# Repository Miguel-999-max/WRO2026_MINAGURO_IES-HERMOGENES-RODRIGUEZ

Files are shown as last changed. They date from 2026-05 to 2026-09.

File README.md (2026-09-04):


# WRO Future Engineers - MINAGURO
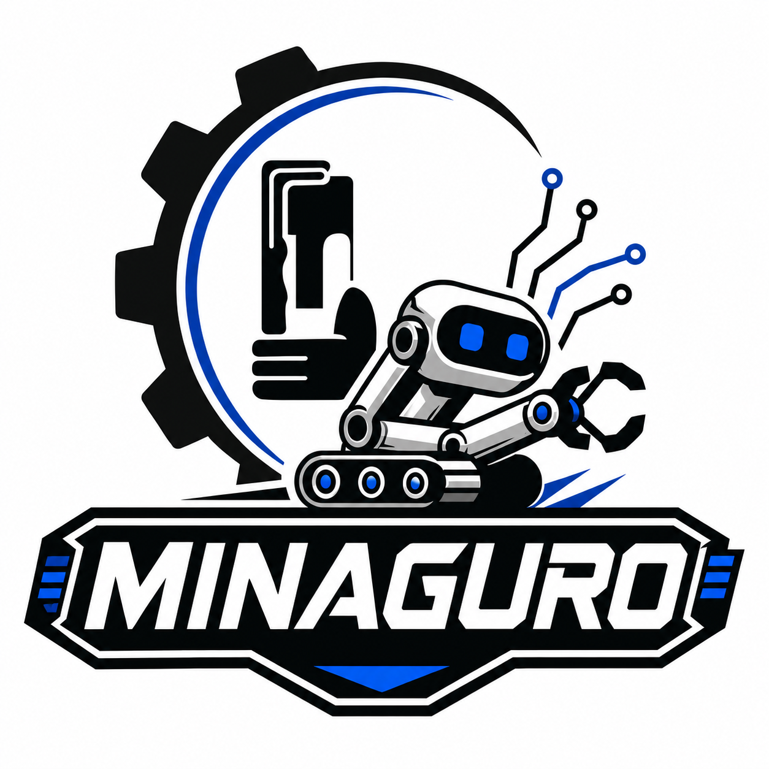
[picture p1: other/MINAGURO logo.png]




<div align="justify">Hello, welcome to the GitHub repository of the <strong>MINAGURO team</strong>, which is competing in the <strong>World Robot Olympiad 2026 Future Engineers</strong> category. Our team is made up of four Spanish students who develop this project on their school breaks with the aim of learning as much as possible.
<br> Guided by our passion for technology, we have created two vehicles. One (the old one), which helped us to get to de national final of the WRO in Andorra; and, another one (the current one), that will perform in the national final. We created the second one motivated by our desire to do it as good as possible and also learn new things and concepts along the way.
<br> Hope you like it!!
</div><br> </br>

> [!IMPORTANT]
> Every time you see this sign (▶&#xFE0E;), click on the text next to it to expand the content!

## 🤝 Sponsors
<div align="justify">We would like to thank our sponsors for making this project possible:

<div align="center">
  <table border="0">
    <tr>
      <td align="center" width="300">
        <a href="https://www.uclm.es/">
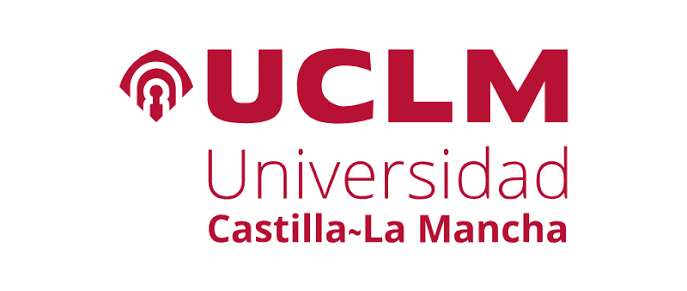
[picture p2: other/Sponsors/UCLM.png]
          <br />
          <b>Universidad de Castilla La Mancha</b>
        </a>
      </td>
      <td align="center" width="300">
        <a href="https://ies-hermogenesrodriguez.centros.castillalamancha.es/">
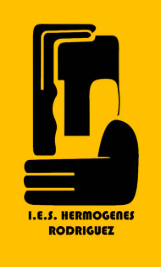
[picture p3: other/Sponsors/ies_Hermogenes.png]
          <br />
          <b>IES Hermógenes Rodríguez</b>
        </a>
      </td>
    </tr>
  </table>
</div>
 
  ## 📁 TABLE OF CONTENTS
* [1. 👥 The Team ](#1--the-team)
* [2. 🤖 Our Robot](#2--our-robot)
* [3. 📝 Daily documentation](#3--daily-documentation)
* [4. 🛠️ Mechanical Design](#seccion-mecanica)
* [5. 🪛 Mobility design](#5--mobility-design)
* [6. ⚡Power and Sensor Architecture](#6--power-and-sensor-architecture)
* [7. 🧠 Strategy](#7--strategy)
* [8. 💻 Software](#8--software)
* [9. 🦾 Build our robot](#9--build-our-robot)

### 1. 👥 The Team
The Minaguro team from Herencia, Spain, is made up of dedicated and hardworking members led by a teacher. This is our first year competing in the WRO Future Engineers category, and each member brings important skills to the team.

<div align="center"><table>
  <tr>
    <td align="center" width="50%">
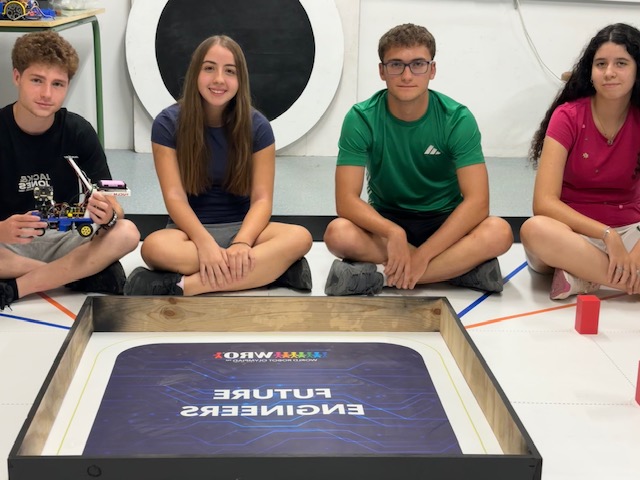
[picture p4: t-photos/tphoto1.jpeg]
      
     team photo
    </td>
    <td align="center" width="50%">
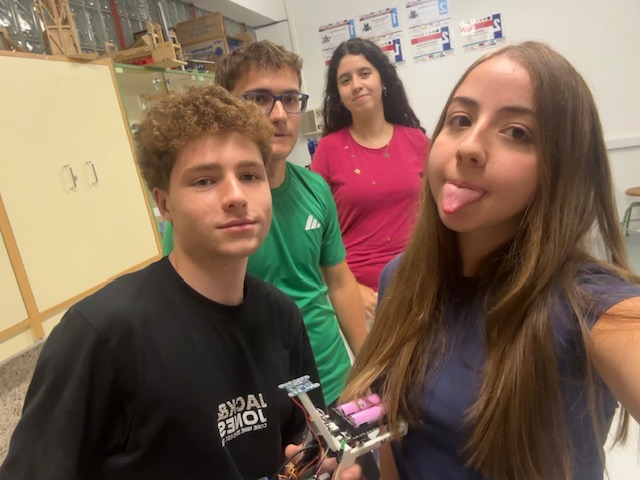
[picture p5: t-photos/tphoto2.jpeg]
      
     funny team photo
    </td>
  </tr>
</table></div>

<br> **Miguel**
<br> **Age:** 17
<br> **Description:** Hi, I'm Miguel from Ciudad Real, Spain, and this is my first time participating in WRO Competition. I have always been into mechanics and robot building, so I didn't hesistate to take up this challenge. I am such a curious and competitive person, and I had put all my efforts in helping the team.

<br> **Natalia**
<br> **Age:** 17
<br> **Description:** Hi, I am Natalia, also from Ciudad Real, Spain, and it is my first time participating, too. I am really good at programming, which I actually enjoy doing. I am hardworking and creative, and this competition, despite being really demanding, has helped me to enter the engineering world.

<br> **Rocío** 
<br> **Age:** 16
<br> **Description:** Hi! I'm Rocío from Spain and this is the first time in the WRO competition. Since I was a kid, I've loved solving puzzles and maths problems. I started to interest in robotics when I was at secondary school, when my teacher taught us how to program. I thougth that was really fun.

<br> **Guillermo**
<br> **Age:** 16
<br> **Description:** Hi, I am Guillermo. I am from Ciudad Real, Spain, and I joined this project because I have always been really keen on I.T. and problem solving. Although this competition has been really challenging, the experience with all the team is worth it.

### 2. 🤖 Our Robot

#### 2.1 Old Robot (Arduino)

<details>
<summary><b>Here are some pictures of our old robot to help with it´s reproducibility:</b></summary>
<br>

<div align="center"><table>
  <tr>
    <td align="center" width="33%">
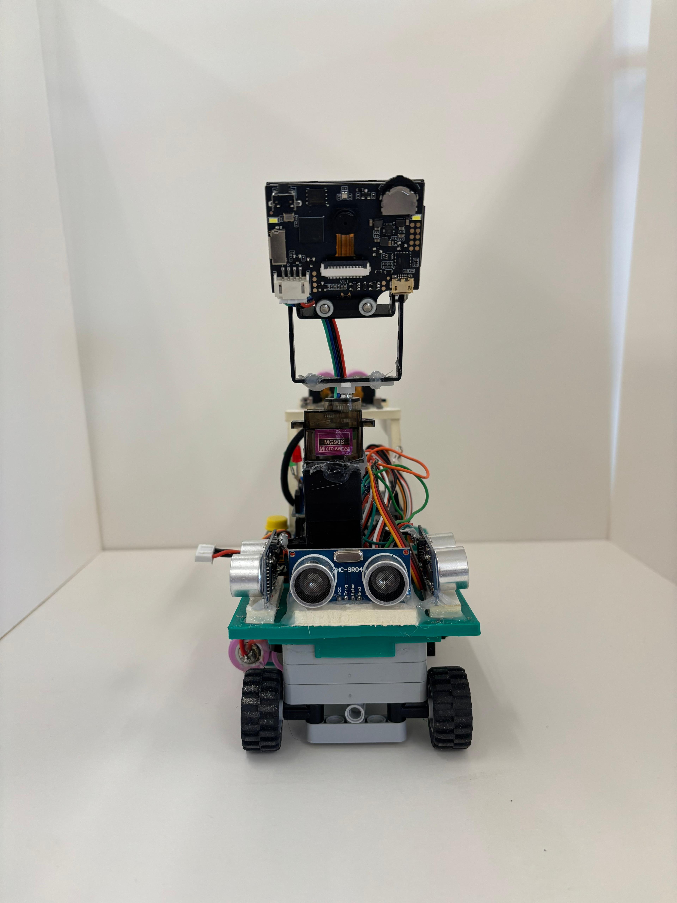
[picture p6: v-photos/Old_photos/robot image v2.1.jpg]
      
     robot´s front view
    </td>
    <td align="center" width="33%">
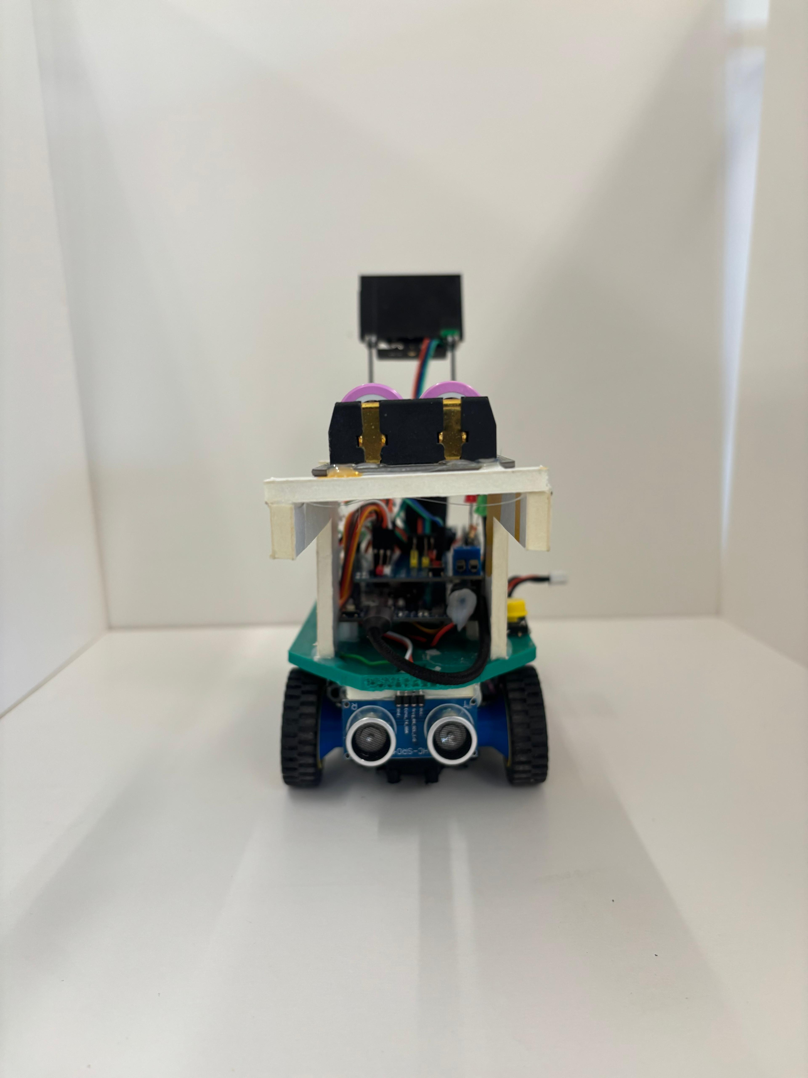
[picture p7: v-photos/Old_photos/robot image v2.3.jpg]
      
     robot´s back view
    </td>
    <td align="center" width="33%">
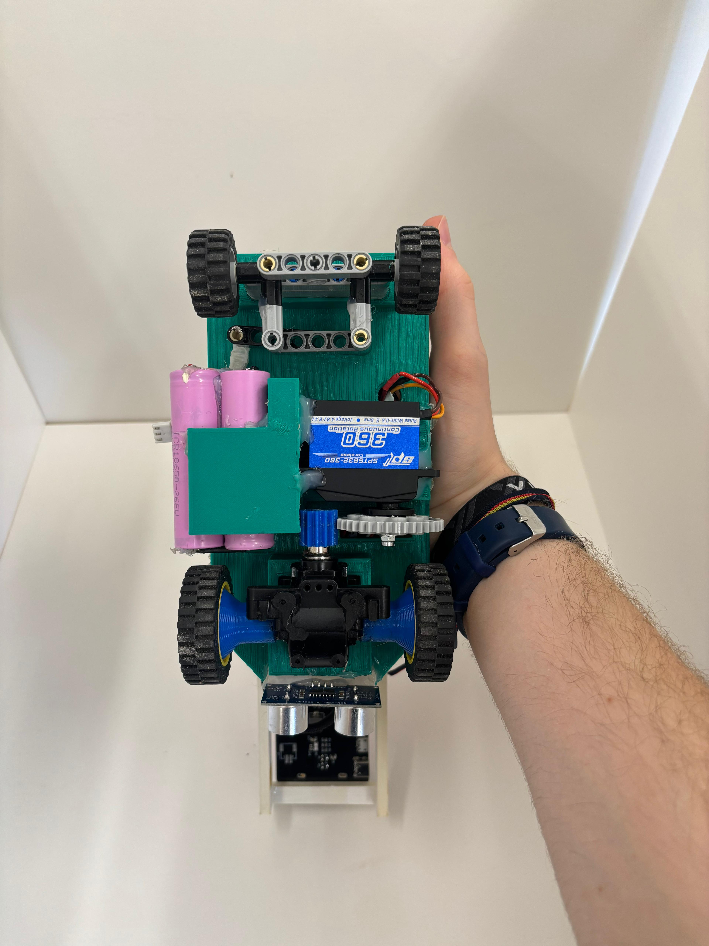
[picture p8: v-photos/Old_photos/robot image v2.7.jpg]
      
     View from underneath the robot
    </td>
  </tr>
</table></div>

<div align="center"><table>
  <tr>
    <td align="center" width="33%">
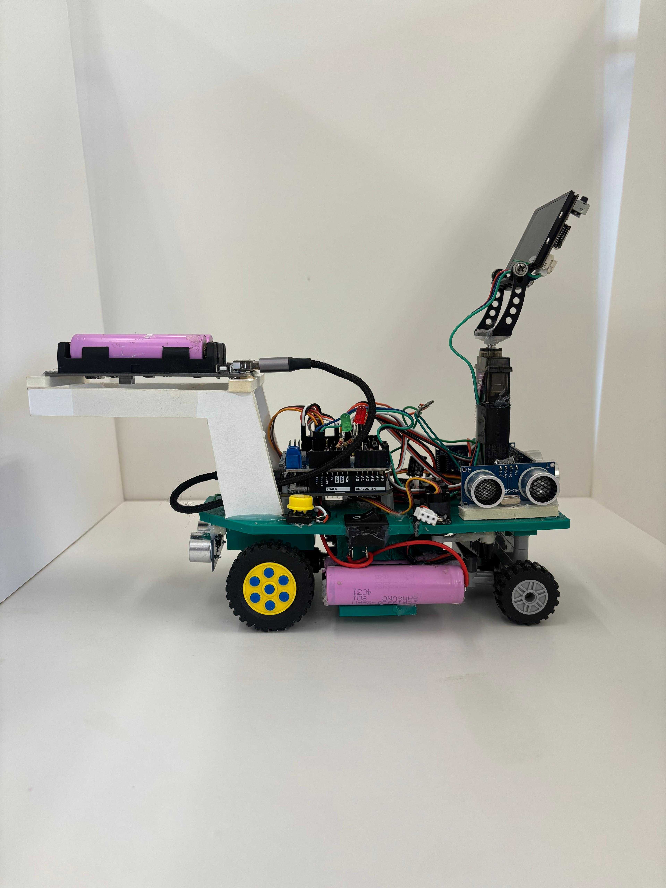
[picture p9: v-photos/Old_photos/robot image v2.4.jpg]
      
     Robot’s right side view
    </td>
    <td align="center" width="33%">
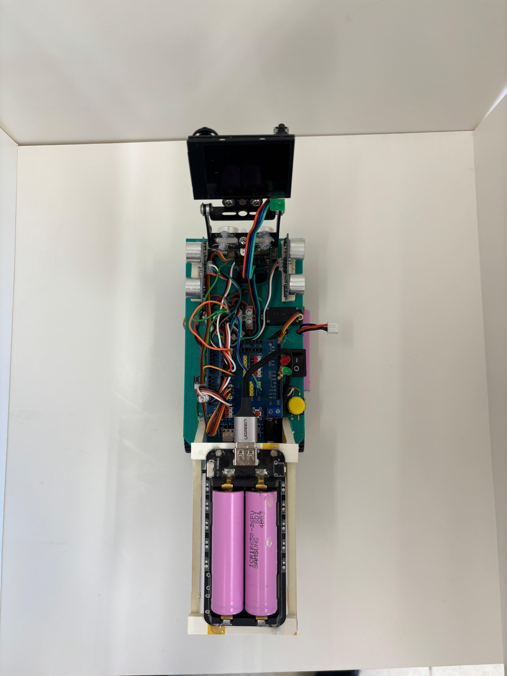
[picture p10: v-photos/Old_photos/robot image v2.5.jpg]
      
     View of the robot's layout
    </td>
    <td align="center" width="33%">
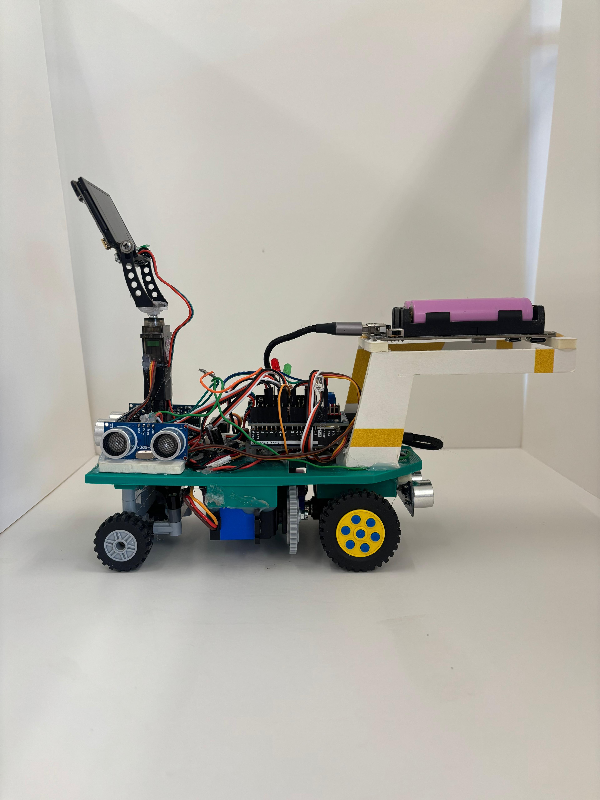
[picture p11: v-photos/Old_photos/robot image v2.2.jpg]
      
     Robot’s left side view
    </td>
  </tr>
</table></div>

<div align="center"><table>
  <tr>
    <td align="center" width="50%">
      <b>Other robot´s views</b><br>
    </td>
<div align="center"><table>
  <tr>
    <td align="center" width="33%">
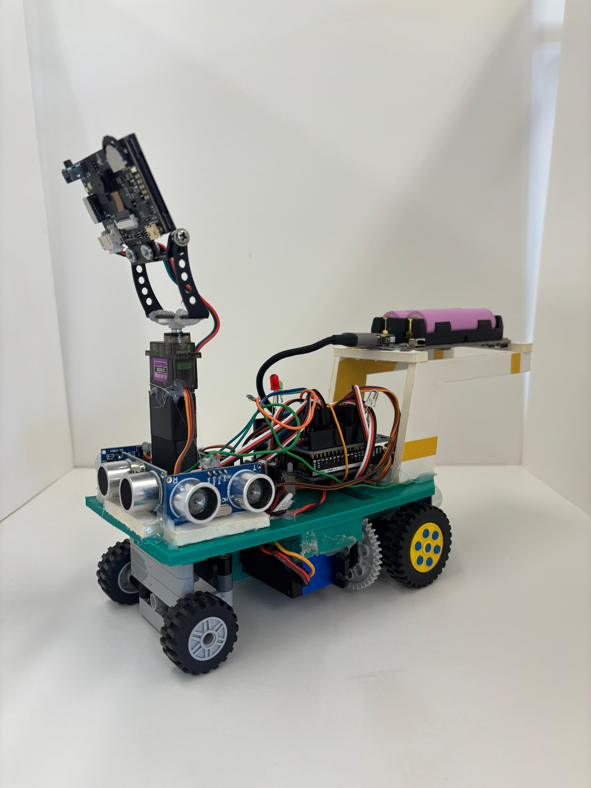
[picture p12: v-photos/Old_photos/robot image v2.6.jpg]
      
    </td>
    <td align="center" width="33%">
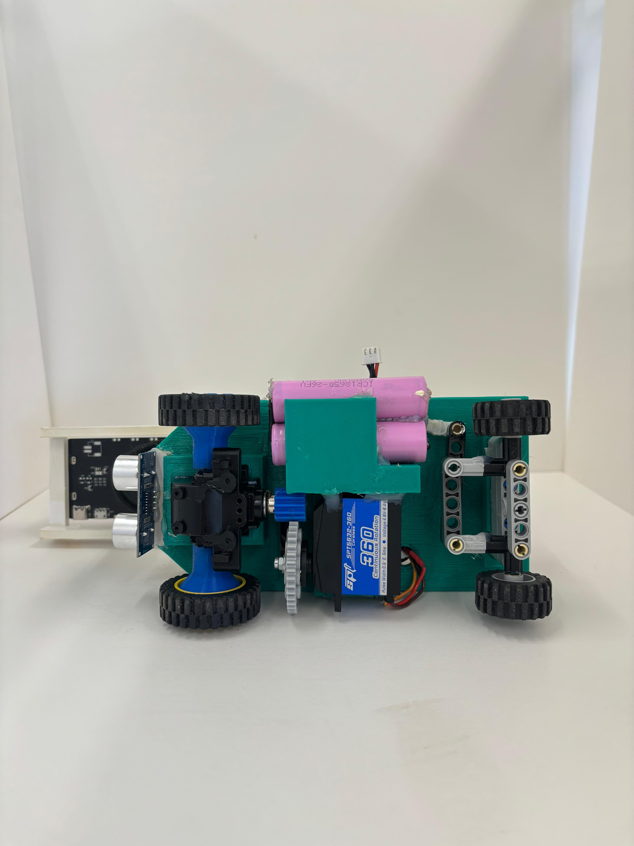
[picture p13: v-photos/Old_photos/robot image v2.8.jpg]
      
    </td>
    <td align="center" width="33%">
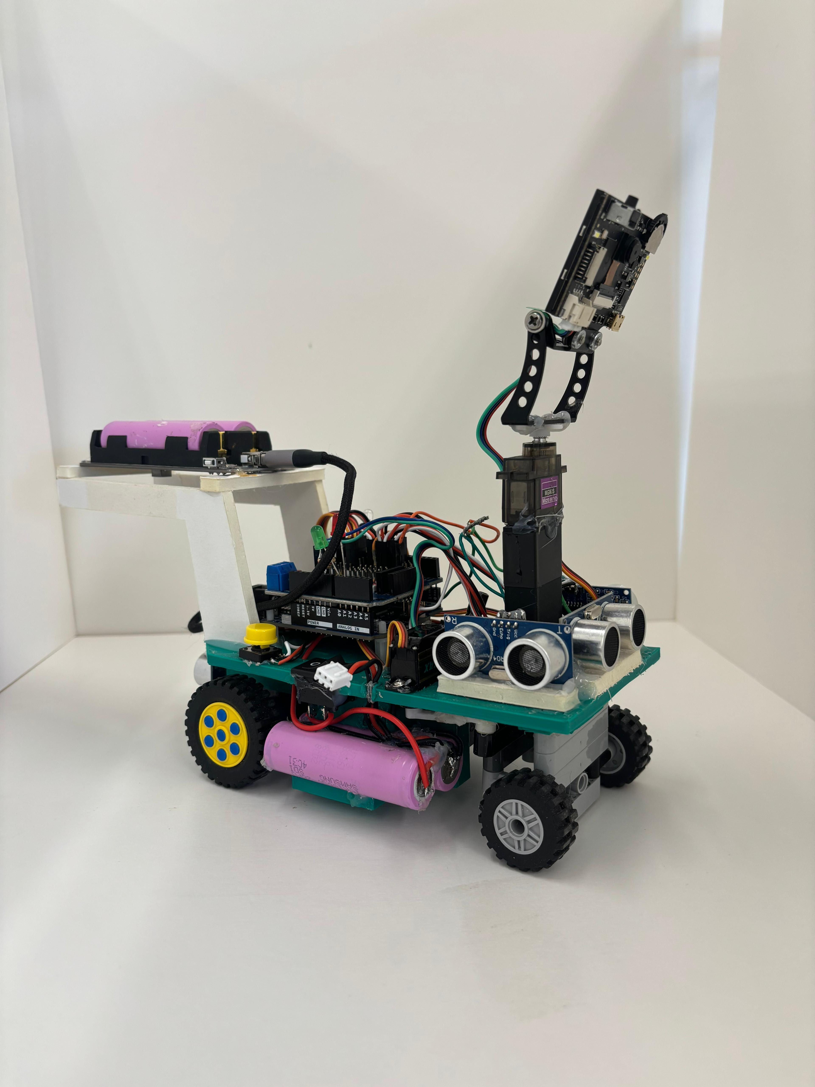
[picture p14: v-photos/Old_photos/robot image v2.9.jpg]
      
    </td>
  </tr>
</table></div>
<div align="center"><table>
  <tr>
    <td align="center" width="33%">
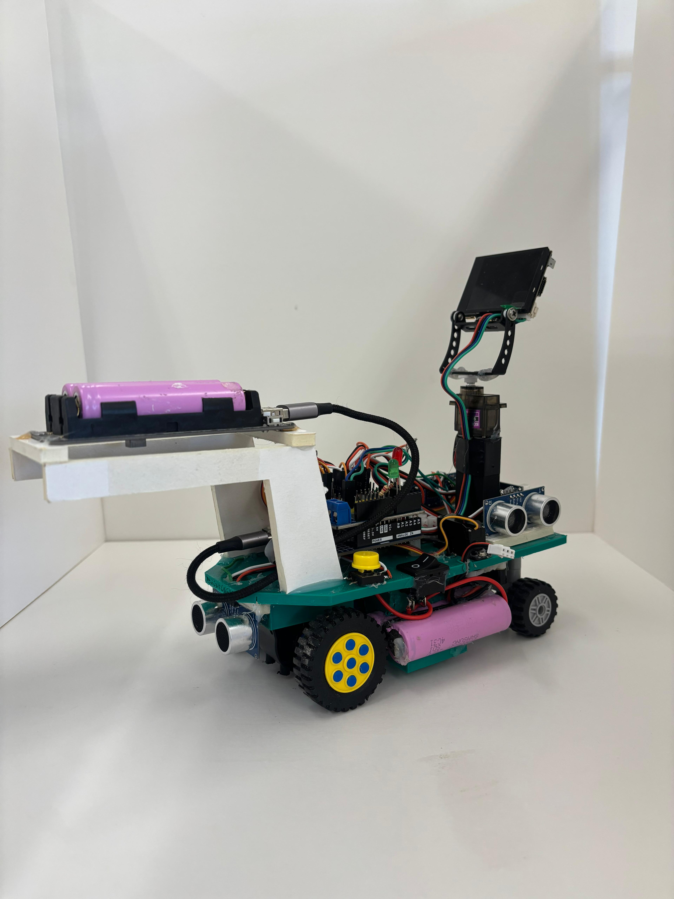
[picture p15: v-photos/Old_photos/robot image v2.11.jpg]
      
    </td>
    <td align="center" width="33%">
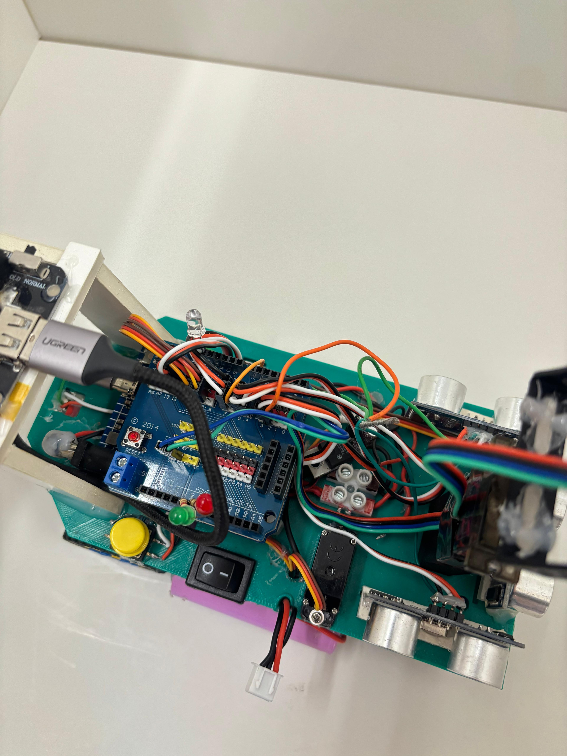
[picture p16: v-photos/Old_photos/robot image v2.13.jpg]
      
    </td>
    <td align="center" width="33%">
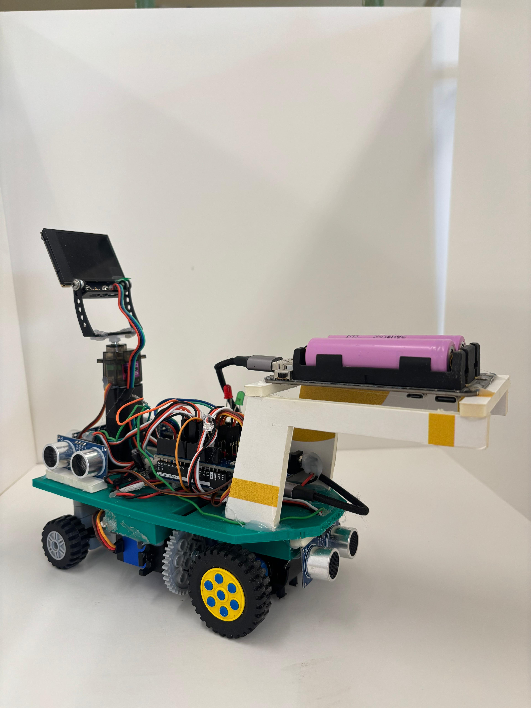
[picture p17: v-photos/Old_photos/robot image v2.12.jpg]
      
    </td>
  </tr>
</table></div>
  </details>
 
#### 2.2 Current Robot (Raspberry)

<details>
<summary><b>Here are some pictures of our current robot to help with it´s reproducibility, and a table listing its main technical specifications:</b></summary>
<br>

<div align="center"><table>
  <tr>
    <td align="center" width="33%">
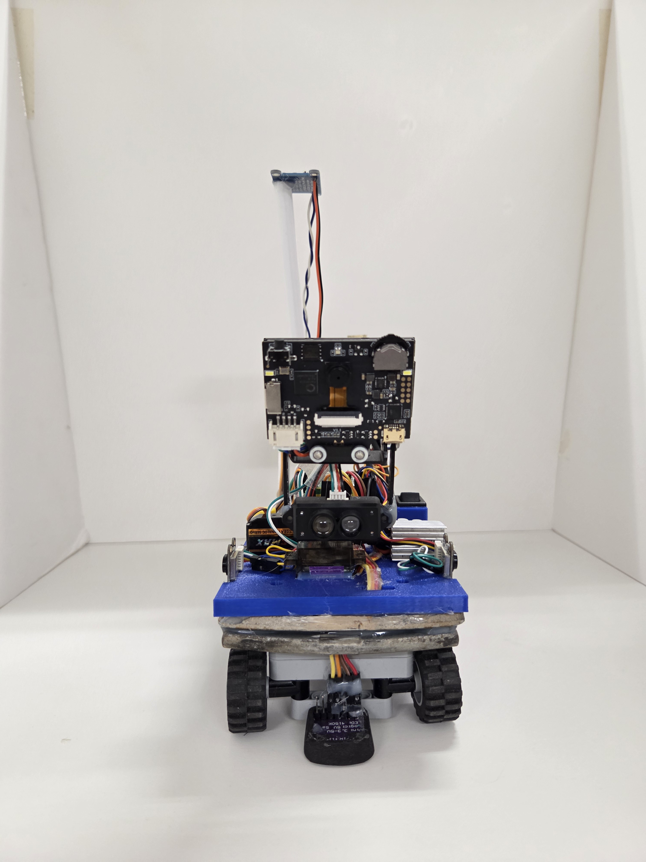
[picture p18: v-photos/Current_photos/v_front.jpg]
      
     robot´s front view
    </td>
    <td align="center" width="33%">
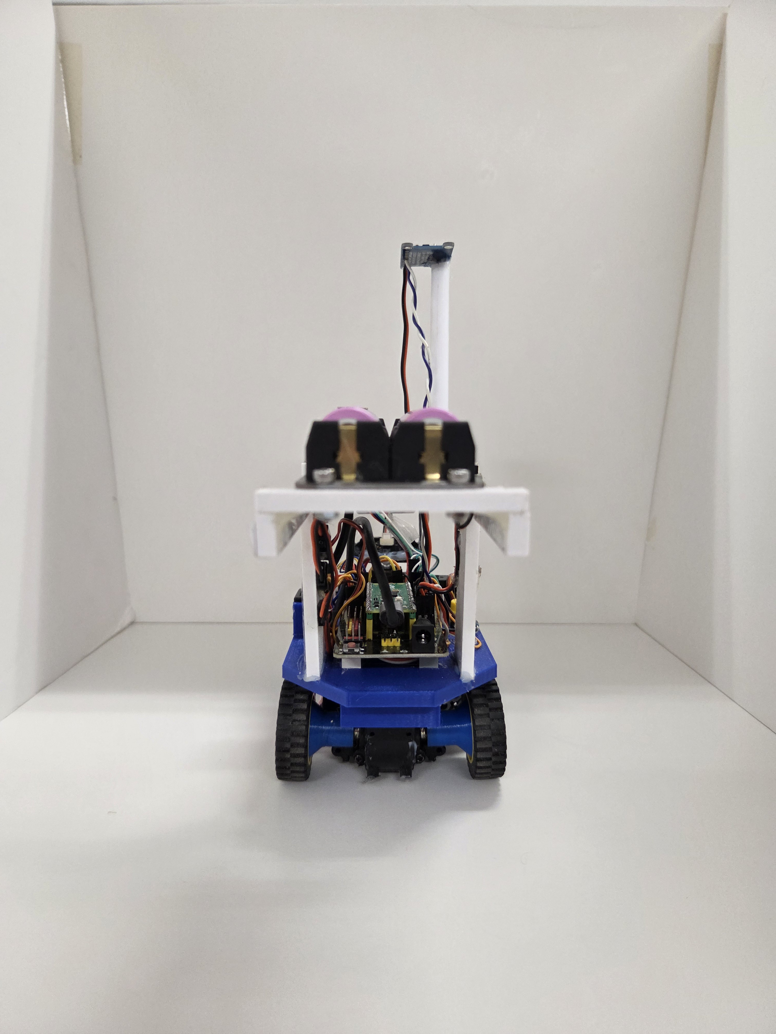
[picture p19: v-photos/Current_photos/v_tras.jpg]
      
     robot´s back view
    </td>
    <td align="center" width="33%">
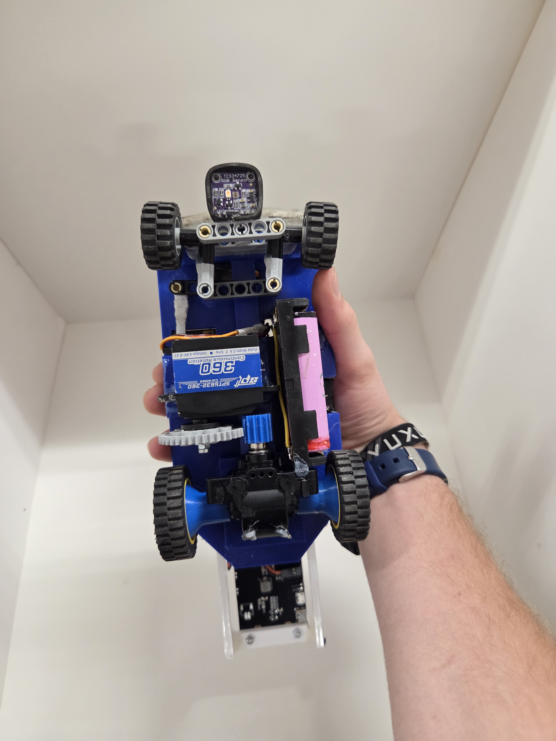
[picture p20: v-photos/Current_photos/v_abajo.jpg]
      
     View from underneath the robot
    </td>
  </tr>
</table></div>

<div align="center"><table>
  <tr>
    <td align="center" width="33%">
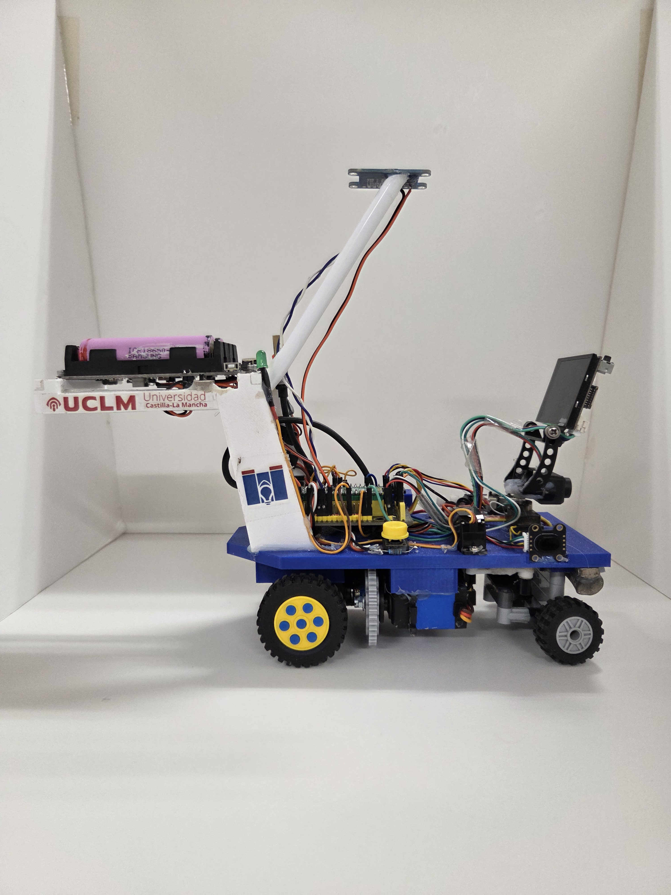
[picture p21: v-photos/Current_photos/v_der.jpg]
      
     Robot’s right side view
    </td>
    <td align="center" width="33%">
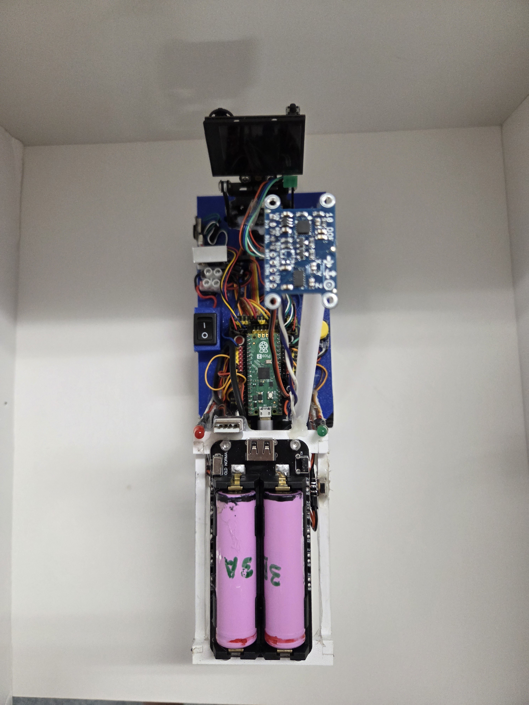
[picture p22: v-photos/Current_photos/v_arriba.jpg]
      
     View of the robot's layout
    </td>
    <td align="center" width="33%">
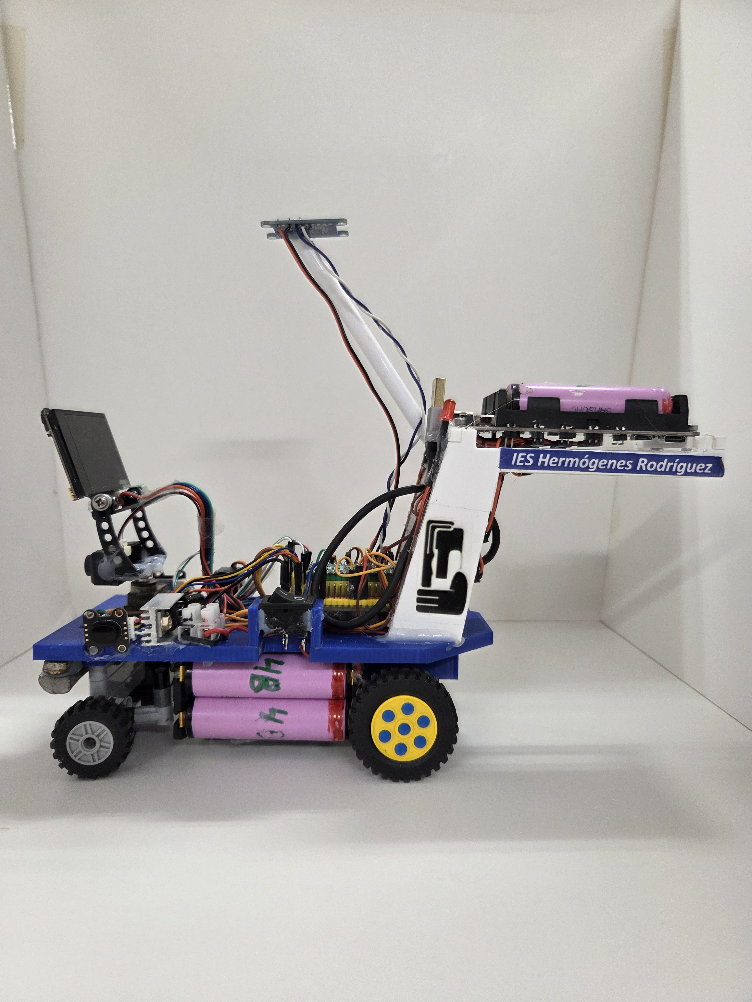
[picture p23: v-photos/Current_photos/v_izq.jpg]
      
     Robot’s left side view
    </td>
  </tr>
</table></div>

<div align="center"><table>
  <tr>
    <td align="center" width="50%">
      <b>Other robot´s views</b><br>
    </td>
<div align="center"><table>
  <tr>
    <td align="center" width="33%">
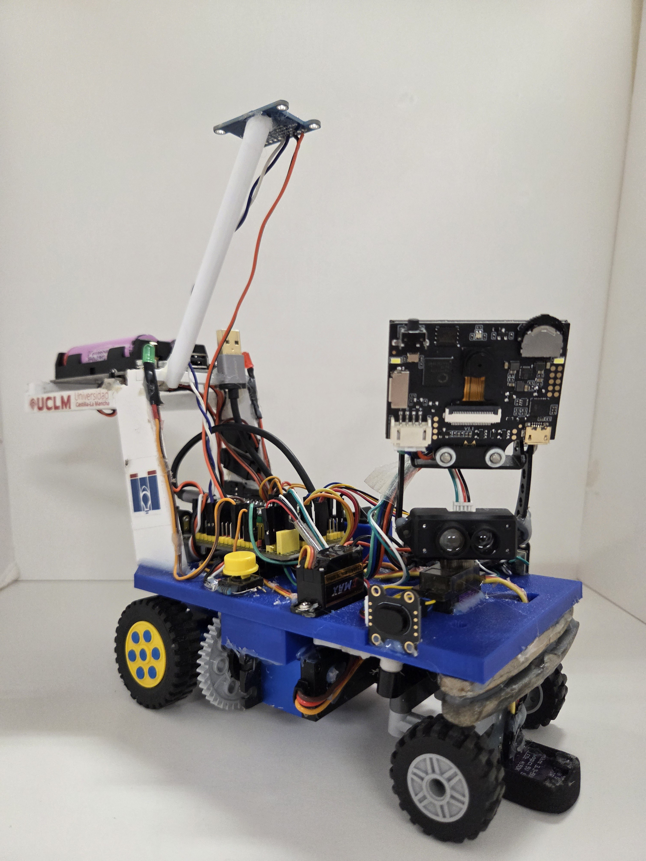
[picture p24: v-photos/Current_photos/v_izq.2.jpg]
      
    </td>
    <td align="center" width="33%">
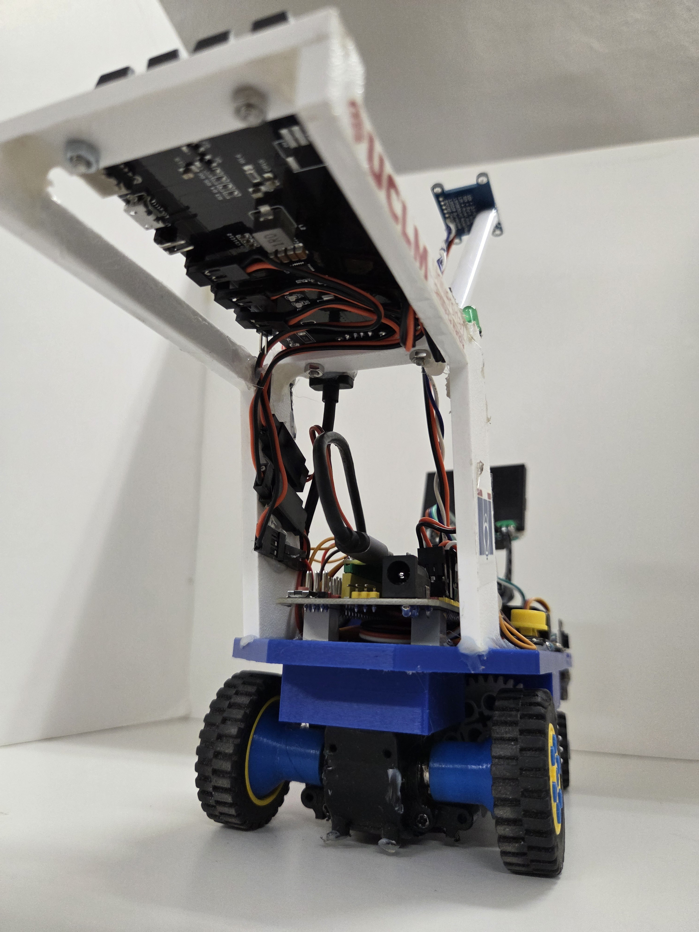
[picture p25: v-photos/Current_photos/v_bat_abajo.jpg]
      
    </td>
    <td align="center" width="33%">
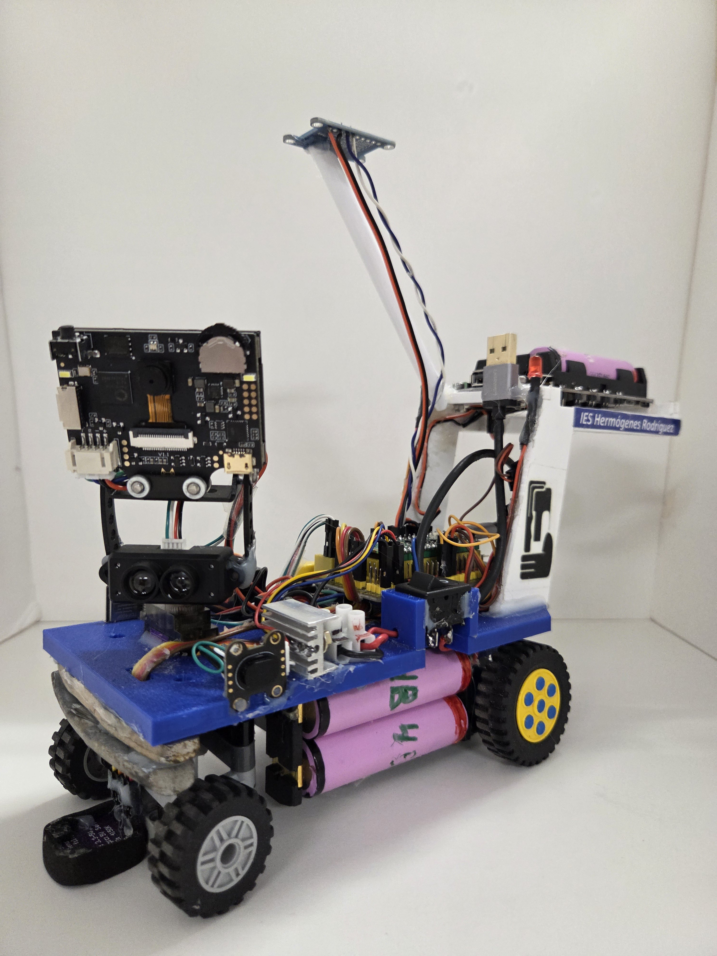
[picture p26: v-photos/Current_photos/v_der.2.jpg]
      
    </td>
  </tr>
</table></div>
<div align="center"><table>
  <tr>
    <td align="center" width="33%">
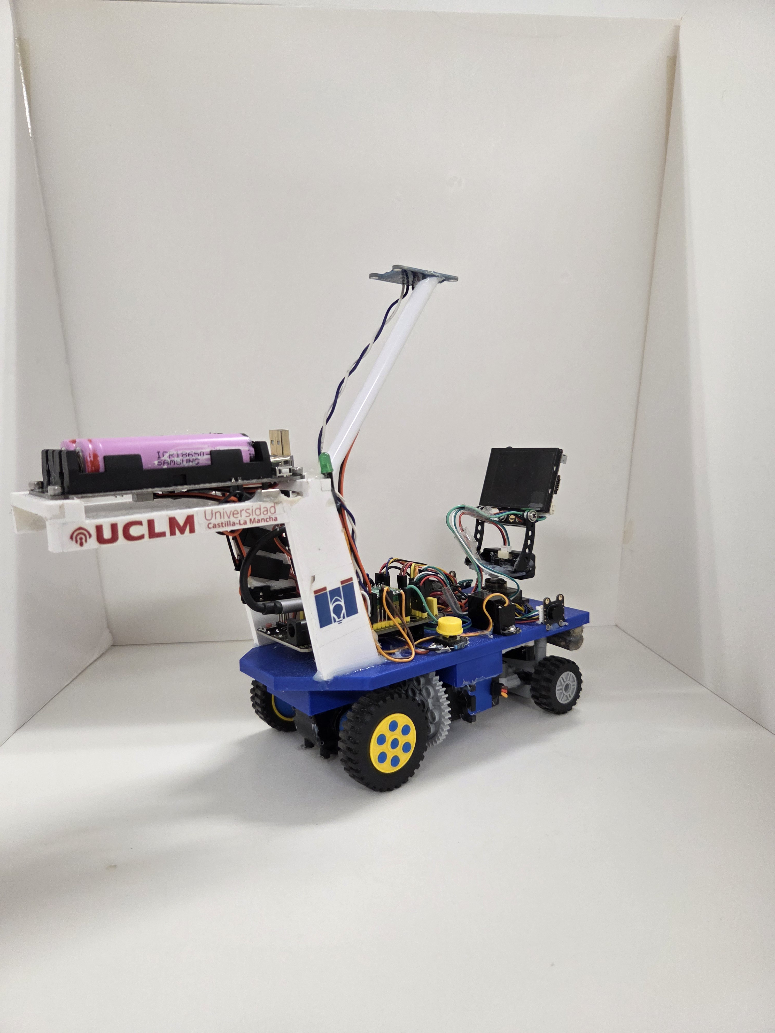
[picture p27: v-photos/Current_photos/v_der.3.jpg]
      
    </td>
    <td align="center" width="33%">
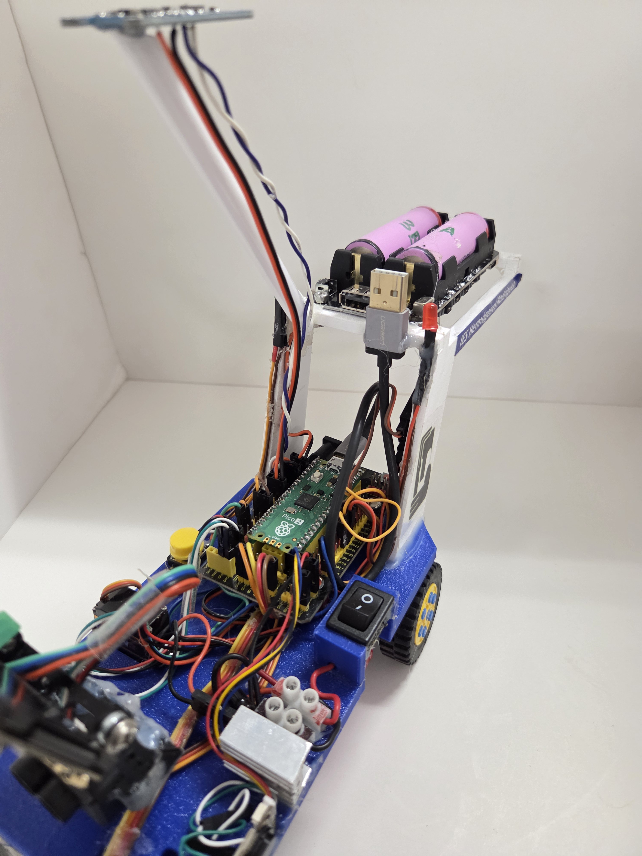
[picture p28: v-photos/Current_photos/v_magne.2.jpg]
      
    </td>
    <td align="center" width="33%">
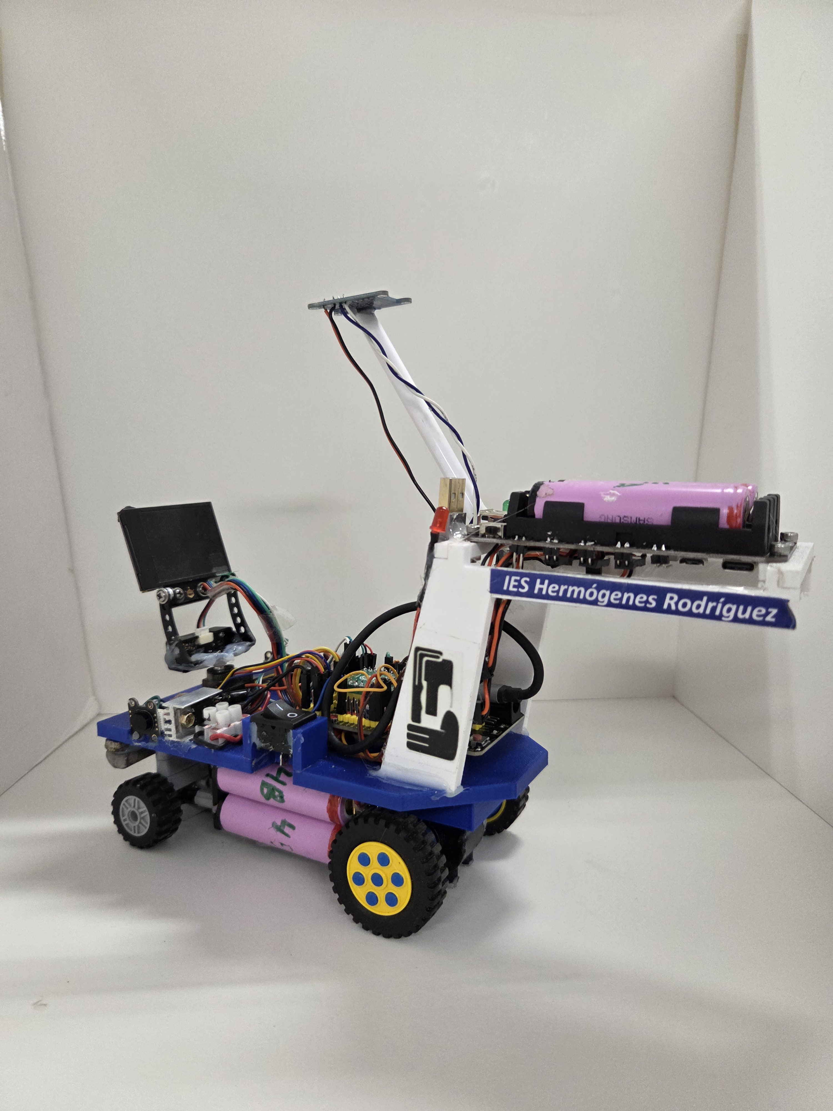
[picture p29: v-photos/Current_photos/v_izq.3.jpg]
      
    </td>
  </tr>
</table></div>

https://github.com/user-attachments/assets/58a79564-a333-4f58-b753-fa61092973e2

<table width="100%" align="center">
  <tr>
    <th align="center">Feature</th>
    <th align="center">Value</th>
  </tr>
  <tr>
    <td align="center">Length</td>
    <td align="center">27,5 cm</td>
  </tr>
  <tr>
    <td align="center">Width</td>
    <td align="center">9,5 cm</td>
  </tr>
  <tr>
    <td align="center">Height</td>
    <td align="center">23 cm</td>
  </tr>
  <tr>
    <td align="center">Weight</td>
    <td align="center">796 g</td>
  </tr>
  <tr>
    <td align="center">Maximum stable speed</td>
    <td align="center">0,211 m/s</td>
  </tr>
  <tr>
    <td align="center">Torque</td>
    <td align="center">2,5-4 N</td>
  </tr>
  <tr>
    <td align="center">Maximum stable revolutions</td>
    <td align="center">1,495 revolutions/s</td>
  </tr>
  <tr>
    <td align="center">Microcontroller</td>
    <td align="center">Raspberry Pi Pico 2</td>
  </tr>
  <tr>
    <td align="center">Vision system</td>
    <td align="center">HUSKYLENS module</td>
  </tr>
  <tr>
    <td align="center">Motor system</td>
    <td align="center">DC motor</td>
  </tr>
  <tr>
    <td align="center">Steering system</td>
    <td align="center">Ackermann steering</td>
  </tr>
  <tr>
    <td align="center">Transmission system</td>
    <td align="center">Gear transmission</td>
  </tr>
  <tr>
    <td align="center">Motor</td>
    <td align="center">SPT5632-360 servo</td>
  </tr>
  <tr>
    <td align="center">Steering motor</td>
    <td align="center">MS18 servo</td>
  </tr>
  <tr>
    <td align="center">Batteries</td>
    <td align="center">Samsung ICR18650-26FU batteries</td>
  </tr>
  <tr>
    <td align="center">Camera processing speed</td>
    <td align="center">11–30 FPS</td>
  </tr>
  <tr>
    <td align="center">Maximum current draw</td>
    <td align="center">1,5 A</td>
  </tr>
  <tr>
    <td align="center">Average lap time</td>
    <td align="center">25 s</td>
  </tr>
  <tr>
    <td align="center">Chassis type</td>
    <td align="center">Custom PCB chassis</td>
  </tr>
</table>

</details>

### 3. 📝 Daily documentation
Here you can find the detailed progress of the MINAGURO team during the tournament:

<details>
<summary><b>🔍 March 2026</b></summary>
<br>
 
* **04/03/2026:** We began dividing up the work among the group, agreeing that Miguel and Rocío would handle the robot and the documentation, and Natalia and Guillermo would handle the programming. We also discussed the general features of the project. After watching videos of models from previous years and given that the robot’s maximum dimensions are 30x20 cm (which we felt was too large), we decided to try to make it as small as possible, since smaller robots tend to be more mobile and would also make it easier to avoid obstacles. Regarding the choice of the base board, we had four options: Raspberry Pi, Arduino R3, and Arduino R4 (with and without Bluetooth/Wi-Fi modules). Of these, we chose the Arduino R4 Minima (without Bluetooth/Wi-Fi) because it has a much faster protocol and more memory, and because the C++ used is a programming language we were already familiar with, which would make it easier for us to program; furthermore, it is compatible with the HUSKYLENS camera we already had and decided to use.  

* **05/03/26:** We started looking for components in our classroom that could be used to build the robot because we must use the free stuff the Councilor of Education of CLM has given to every school to ensure a level playing field. We also researched strategies from previous years on GitHub. 

* **06/03/26:** We decided on a basic strategy for the first and second challenges:  
  * First challenge:</ins> do not use HUSKYLENS; navigate as close as possible to the interior partitions to speed up the process; detect walls using distance sensors.  
  * Second challenge:</ins> use HUSKYLENS to detect obstacles and record their color, and distance sensors to measure the distance to the walls. 

* **09/03/26:** We researched the best way to move the robot; to do this, we looked at different models of remote-controlled cars, past projects we found in class, and GitHub repository files. In the end, we concluded that it would be best to have four wheels: two in front to control steering and two in the back to move it.  

* **10/03/26:** While reading the contest rules, we ran into a problem; we realized we couldn’t use a motor for each wheel, so we explored how we could drive both wheels with a single motor while still allowing them to operate independently in order to navigate curves. Ultimately, we agreed that the best solution would be to use a mechanical differential.  

* **11/03/26:** We searched and asked acquaintances for a differential or an old remote-controlled car to use in the project. Since no one had one, we started looking on different websites for a cheap, small differential that we could use for our robot. Finally, we settled on a front-axle differential from a remote-controlled robot that we found on AliExpress (even though we’ll be using it for the rear axle, since that doesn’t affect us) because it’s standard quality, inexpensive, and shipping isn’t too slow.  

* **12/03/26:** We discussed the distance sensors we’re going to use. In class, we have the following types: 
  * HC-SR04:</ins> ultrasonic distance sensor, works at a distance of up to four meters, digital pin connection, less accurate, sensitive to different types of surfaces and noise, very bulky.   
  * CJVL53L0XV2:</ins> laser distance sensor, works at a distance of up to two meters, I2C connection, high precision, compact, very low power consumption.  
  * TOF10120:</ins> laser distance sensor, operates at a range of up to 1.8 meters, I2C and UART connectivity, fast readings, large 10cm blind spot.  
With all this in mind, we decided to try the CJVL53L0XV2 laser sensors, as they offer the most benefits; we also decided to use three of them (one in front and two on each side) so we can measure the distance to the exterior walls at the front and the distance to the central partition on the sides.  

* **13/03/26:** We remembered that both HUSKYLENS and the laser distance sensors use the I2C protocol, so we decided to check that the addresses they use do not conflict. Once we verified this, we realized we had forgotten that, since the three distance sensors we plan to use are identical, they all use the same address. After writing a program to change the bus address and failing to get it to save, we agreed that having to change the address every time the program starts would waste time and add complexity to the program; so we decided to come up with another strategy individually and then pool our ideas.  

* **16/03/26:** After pooling all our ideas, we decided that the best option would be to use the HC-SR04 distance sensors, which, although less precise, we were already familiar with—an advantage when it comes to programming. Meanwhile, we began studying the HUSKYLENS AI camera, specifically its different modes, to see which one would be most useful to us. 

* **17/03/26:** We discussed how we could power the robot. We have eight rechargeable lithium batteries (model SAMSUNG ICR18650-26FU). We used this type of battery last year to build a PRINTBOT Evolution BQ robot, so based on that experience, we considered the best way to use them to ensure optimal battery life and minimize the space they occupy. We’re going to connect two cells in series to get 3.7 + 3.7 = 7.4 V, although when fully charged they actually reach 8.4 V. However, that voltage is ideal for powering the Arduino via Vin and for powering the drive servo directly from the batteries. For the Huskylens module, we plan to power it from the Arduino, but we’ll need to run tests because it has high power consumption. As for capacity, we need to look at the power consumption of each component and add them up to see how long they’ll last. 

* **18/03/26:** We looked for LEGO pieces in the sets we have in class for both the drive and steering wheels, as well as for the front-wheel steering system. To design the latter, we drew inspiration from how the steering systems of most remote-controlled cars are built and created a diagram of how we could assemble it using the pieces we have.   

* **19/03/26:** We assembled the steering system using LEGO pieces and a servomotor we had in class. Additionally, since we had already reviewed all of HUSKYLENS’s functions, we agreed that the most useful ones would be object recognition and color recognition, so we began researching these in greater depth and studying the library we found in its GitHub repository. 

* **20/03/26:** We created a program to rename the objects and colors we captured with the camera, since we thought this would make it easier to refer to the objects both within the rest of the program and visually on the camera screen. In doing so, we realized we had a problem: when we set HUSKYLENS to object detection mode, it always detected an object, even if the recorded objects weren’t visible. Since in this mode HUSKYLENS always had to have an object located, even if it didn’t exist, we decided it would be better to forget about using it and change our strategy for the second challenge. We will try to complete it by using the distance sensors both to maintain the distance from the central wall and to detect obstacles and steer toward them, and HUSKYLENS to determine the color of said obstacle. 

* **23/03/26:** Since we received the differential, we’ve been testing it; in doing so, we noticed that because it was new, the gears had trouble meshing properly—in other words, it didn’t run smoothly and fluidly. So we took it apart, lubricated it, and wore down the gear teeth by spinning them with a drill. On the other hand, since we now have the differential, from all the wheels we managed to collect, we chose the ones that worked best with both mechanisms. Finally, for the drive wheels, we chose larger ones because the bigger the wheels, the further the robot moves, and to match the size of the differential; and for the steering wheels, we chose smaller ones because we didn’t have any others of the same size. 

* **24/03/26:** We attached a 360° servo motor we have in class to the differential to check its speed, and we all agreed that it was moving too slowly. Therefore, we decided to increase the speed using a gear system. To do this, since we don’t have any gears that fit perfectly with the differential, we decided to design one in 3D and attach another one from the classroom LEGO kit. We also took the opportunity to design some couplings to attach the wheels to the differential.  

* **25/03/26:** We continued working on the 3D designs and researching HUSKYLENS. 

* **26/03/26:** We continued working on the 3D designs and created a program that moves a servo when HUSKYLENS detects an object in the center of the camera’s field of view; we did this simply to test whether we can use the camera to determine the object’s position in addition to detecting its color. 

* **27/03/26:** We finished the 3D designs and sent them to print on the school’s 3D printer. Additionally, after creating the previous program, we decided it might be a good idea to use coordinates instead of the object’s approximate position; therefore, we wrote a program that displays the center coordinates on the serial monitor.

</details> 

<details>
<summary><b>🔧 April 2026</b></summary>
<br>
 
* **08/04/26:** We drew a diagram of how we want to assemble our robot and how we’re going to arrange all the components. We placed the HUSKYLENS at the front to detect colors, positioned a distance sensor on each side so we can measure using any of the four depending on what’s most useful, and placed the batteries under a platform with the wheels (and their respective servomotors), since this saves space and allows us to arrange the board and components more neatly above that platform. On the other hand, we considered different material options for the base, such as wood, plastic (3D printer), and a sheet of foam board we found in class. In the end, we decided that the foam board was the best option, since wood was very difficult for us to work with and would take more time, and 3D printing would also require a significant time investment (which would reduce our ability to test the program) and require us to have a clear understanding of all the component positions (something we weren’t 100% sure of yet). Even so, we decided this would be a temporary solution, and once we had everything figured out, we would make a 3D-printed base. 

* **09/04/26:** Using a clamp meter, we measured how much power our robot would consume to determine whether we could use the battery module we had chosen. We found that the HUSKYLENS camera uses between 230 and 420 mA, the Arduino R4 board consumes 100 mA, the HC-SR04 consumes 15 mA, the microservo consumes 200 mA, and the RC servo consumes 700 mA. Therefore, our robot would consume a total of 1215 mA, which would give us just over two hours of runtime. Theoretically, that would be the robot’s total power consumption, but in reality, we measured that the robot consumes 500 mA, so those batteries, which have a capacity of 2600 mAh, should power the robot for more than 5 hours. Meanwhile, we began preparing the wiring for the distance sensors and the servo motors. However, we noticed that the Huskylens module sometimes reboots. We think this is because the Arduino board isn’t able to provide enough power, and we can’t connect it directly to the batteries since the module doesn’t support 8.4 V. While searching for information, we found a type of regulator called the LM7805 that steps down the voltage to 5 V. We’ve decided to use it to power the Huskylens module.  

* **10/04/26:** We assembled the robot on the temporary base, trying to pack all the components as tightly as possible. We used hot glue because we had it in the classroom; it bonds strongly to the components we’re using, allows us to attach and detach components easily, and doesn’t damage them. During assembly, we had to cut a hole in the board to mount the 180° servo so it would align with the height of the wheels. Once the entire robot is assembled, we create a program to control it with a joystick and check the maximum and minimum values for each servo. The data we have for the servo are: 
  * Voltage: 4.8–8.4 V / Imax = 1.2 A / Maximum torque: 14 kg·cm / N = 72 rpm  
  * For the transmission, we have tested various LEGO gears. The differential has a 12/30 reduction ratio, meaning it reduces the speed by a factor of 2.5. Therefore, we need to multiply the speed between the servo and the differential. Through testing, we found that with a 40-tooth gear on the servo and a 13-tooth gear on the differential input, the vehicle achieves an appropriate speed—neither too fast nor too slow.  
  * Wheel speed calculation: V = 65 × (40/13) × (12/30) = 80 rpm = 1.333 rev/s  
  * The wheels have a diameter of 43 mm and a circumference L = π × 43 = 135 mm  
  * The vehicle’s speed is V = 1.3333 × 0.135 = 0.18 m/s. We have verified this data with a stopwatch, and it is correct. 

<div align="center"><table>
  <tr>
    <td align="center" width="33%">
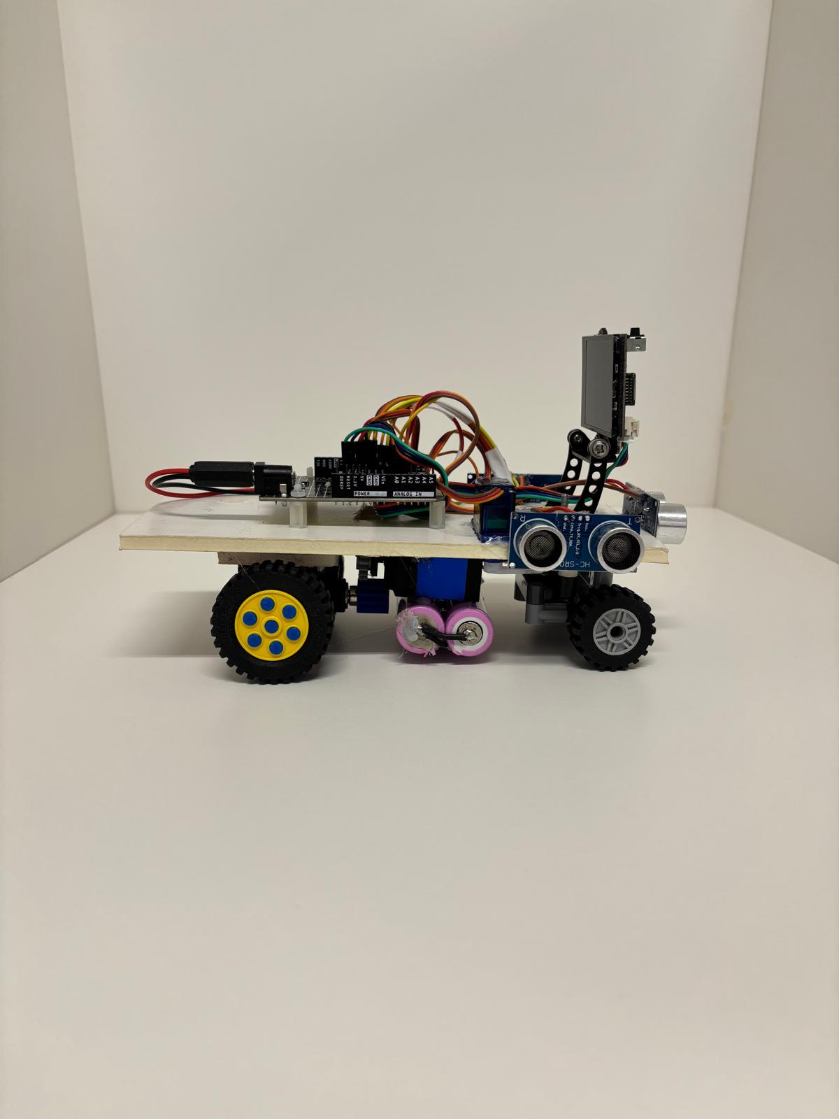
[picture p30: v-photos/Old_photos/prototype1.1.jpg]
      
    </td>
    <td align="center" width="33%">
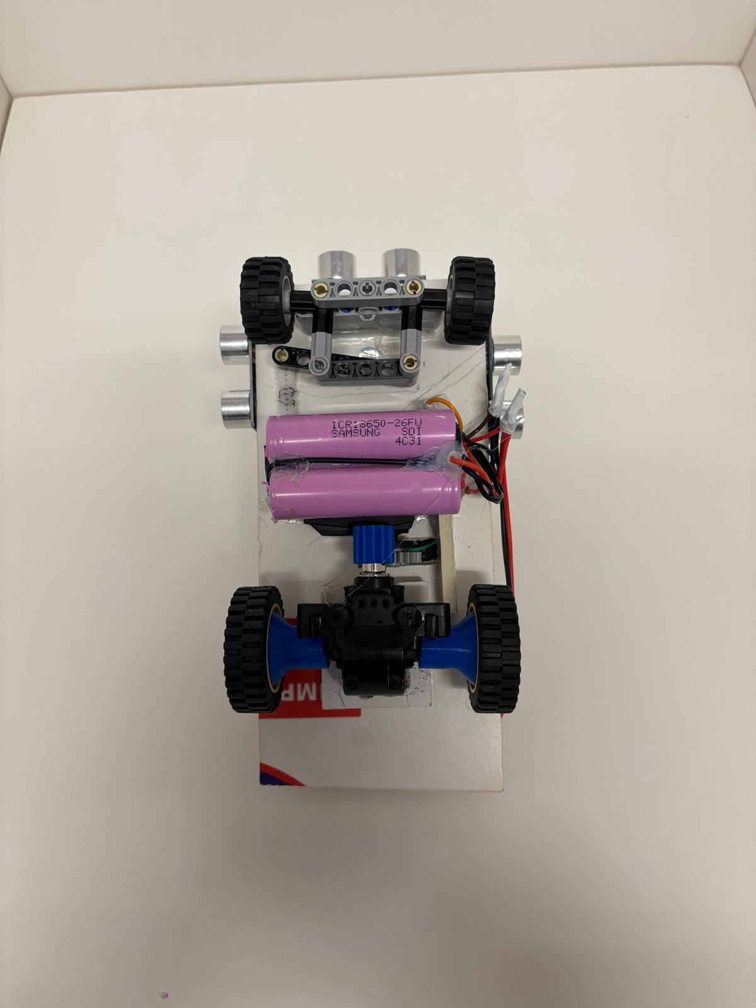
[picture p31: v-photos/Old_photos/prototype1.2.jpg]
      
    </td>
    <td align="center" width="33%">
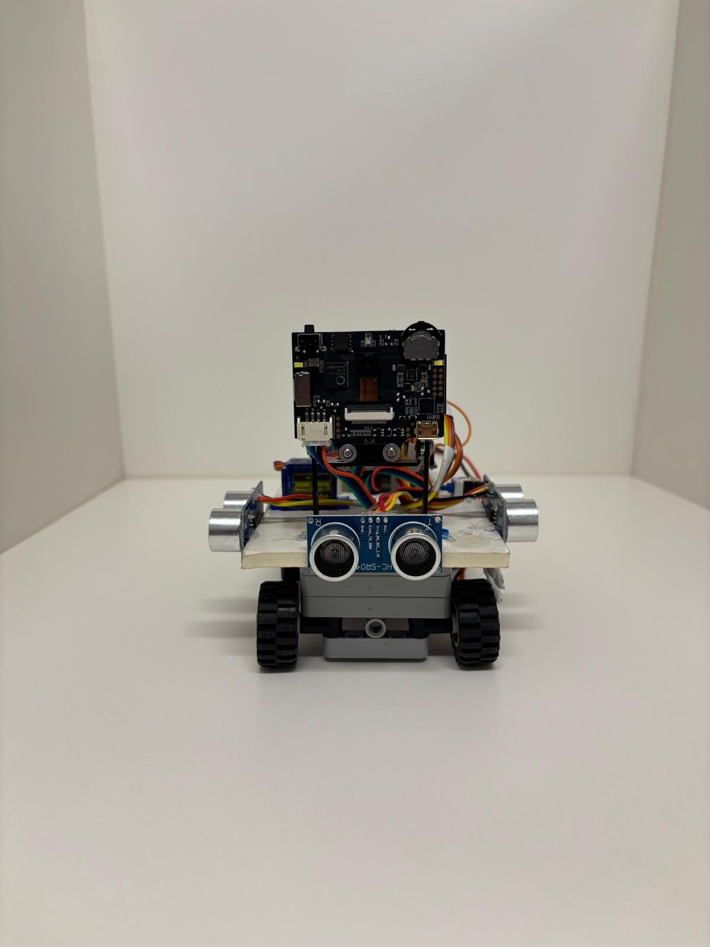
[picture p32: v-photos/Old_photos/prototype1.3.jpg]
      
    </td>
  </tr>
</table></div>

* **13/04/26:** We wrote a program using the distance sensors to make the rear servo move when an object is detected. In doing so, we realized that the library we had always used for these sensors isn’t compatible with the Arduino R4 Mini board, so we looked for another one. The other library we found that was compatible required a common pin to connect all the “triggers” from all the ultrasonic sensors. To do this, we rewired the setup by soldering all the trigger wires from the three sensors together and connecting them to a single pin.

* **14/04/26:** We started creating a basic program to try to navigate around the inside of the parking garage. As we continued testing the programs, we noticed that the robot was moving slower than we’d like, so we decided to increase its speed using a LEGO gear system we have in class. When we incorporated it, we saw that it wasn’t working well because the robot was turning jerkily, so we had to reduce the speed a bit. We thought it was a software issue, so we’re trying to fix it. 

* **15/04/26:** We were unable to fix the error by modifying the code, so we decided to change the gear system, this time using only one gear; as a result, it now moves slower than before, but faster than it did at the start. We also added a servo to the HUSKYLENS, as we believe it’s a good idea to use one because we think it has a narrow field of view, and with the servo attached, we’ll be able to rotate the camera and widen the angle. As for the program, the robot manages to turn around, but it makes very sharp turns, and when it gets too close, it crashes into the wall; we’re going to try to fix that. 

* **16/04/26:** We continue to plan our programs with the possibility of starting either to the right or to the left in mind, trying to check which way we’re going before leaving the parking lot. We have also added another HC-SR04 sensor at the rear to measure the distance to the parking space divider, making it easier for the program to exit the parking space. 

* **17/04/26:** We continued working on the programs, while also exploring options for exiting the parking lot; to do this, we drew inspiration from how participants in previous years had parked. During this process, we came across a robot that used a plastic rod that didn’t interfere with obstacles but allowed it to extend the robot’s length—and, therefore, the length of the parking space. Since we liked this idea, we decided to implement it and devise a parking strategy, taking into account that we now had a greater distance than we initially thought. With that in mind, we decided to create a program. 

* **20/04/26:** Since the front wheels keep jerking, we thought the 180-degree servo might be experiencing interference, so we decided to replace it with a better one we already had. It seems to work better, but it still malfunctions quite a bit. As for the program, we managed to get it to exit the parking space; so all that’s left is to have it face the central partition. We also tried using a magnetometer (compass) from class to get a reading of the robot’s position, with the idea of using it for various tasks like exiting the parking lot or making more precise turns. However, upon checking the readings, we saw that the coordinate intervals weren’t consistent and, therefore, didn’t match reality; we decided to order another one. 

* **21/04/26:** To try to fix the jerking issue, we installed some laser distance sensors and disabled the ultrasonic sensors. We tested them using a box (as if the box were the center of the board), and it worked quite well most of the time, except for a few instances where it didn’t read the position correctly. Next, we tested it on the official competition board; this time, 70% of the time it didn’t read the curves correctly and didn’t take the right direction. After further testing, we concluded that the problem with these sensors was the reflection of light off the black paint on the walls; therefore, they didn’t solve our initial problem. 

* **22/04/26:** We realized that if we connect HUSKYLENS directly to the board, the robot keeps stopping because the Arduino isn't able to power HUSKYLENS properly, causing it to reboot. From now on, we’ll power HUSKYLENS directly from the batteries using a voltage regulator based on the LM7805 circuit, which converts the batteries’ 8.4 volts to 5 volts—enough to power the camera on its own. On the other hand, since we had made so many changes to the robot’s chassis, the base was no longer stable or secure; so we decided it was time to design the final version in 3D. We drew a hand-drawn sketch of where the components would be placed and began designing it in 3D. 

* **23/04/26:** We continued working on the chassis design.  

* **24/04/26:** We are proceeding to replace all the sensors. We have once again used hot glue for the same reasons: it provides a strong, quick bond, is easy to apply and remove, and does not damage the components. In the process, we encountered several design issues that we resolved manually by removing material with a soldering iron to heat and melt the material into the desired shape, since we didn’t have enough time to redesign and print another part. Even so, we will redesign it in 3D so that the robot is perfectly reproducible. Also, since we were going to change the base, we decided to switch the gear ratio to a larger one to reduce the speed slightly. 

* **25/04/26:** We continued assembling the new base and also replaced some of the component cables. We decided to attach the distance sensors to a foam board using hot glue, since hot glue allows us to attach and remove the components easily without damaging them. 

* **27/04/26:** We installed the new magnetometer on the robot using a foam board rod to prevent interference issues and added an LCD display so we could view its readings without having to connect to the computer; once this was done, we began testing. The first few tests went well, but after about 10, it stopped working; we also tried the other one that came with the purchase, and the problem was the same as with the first one. We agreed to try one last time, so we ordered one final magnetometer.  

* **30/04/26:** We no longer have time to move forward with the challenge, so we began preparing all the documentation.

</details> 

<details>
<summary><b>🏆 May 2026</b></summary>
<br>

* **04/05/26:** We are still working on the documentation. 

* **19/05/26:** We are working on the final program and retouching the documentation.

* **26/05/26:** We reviewed what happened during the provincial round, as we had several execution errors due to a misinterpretation of the rules. We reread all the rules carefully and revised our strategy. In the free challenge, the robot starts from a specific zone within the region; whereas, in the obstacle challenge, there is the option to start from that same zone or from the parking area. We decided to take advantage of this option to differentiate the type of challenge the robot is facing.
  * Free challenge: we start from the required zone, “unpark”, complete the laps, count lines to stop, and “park”. All of this is done primarily using distance sensors, with the exception of line counting (for which we use HUSKYLENS).
  * Obstacle Challenge: we start from the parking spot, unpark, drive around while avoiding traffic lights, count lines to stop, find the parking spot, and park. All of this is done primarily using HUSKYLENS.<br>
  Once we’ve clarified all this, we get to work. Since the open challenge was almost complete, we redesigned the part about pulling out of the parking spot (which works for us); so all that would be left is counting the turns and parking, but since we don’t have time, we decided to prioritize solving the obstacle challenge.
* **27/05/26:** After testing the HUSKYLENS, we found that I2C communication causes fewer problems than using the serial port. Additionally, we decided to point the HUSKYLENS downward because when we first set it up, it was detecting colors and shapes outside its field of view, causing frequent errors. In light of this, we also positioned it higher to widen its field of view so it could see obstacles from a greater distance and detect them sooner. Additionally, we encountered an issue with the Arduino R4 Minima board (it stopped working); we believe it may have been caused by a power surge, but we’re not certain. Therefore, we decided to use the Arduino R4 board with Wi-Fi/Bluetooth that we had in class, without using its Wi-Fi and Bluetooth modes since that’s not permitted. As for the software, we first tested a program to count laps that we had already created but never got around to testing. After making some changes, we saw that it worked, so we decided to add it; however, as we mentioned yesterday, we decided not to deviate from the plan, to leave the parking part for later, and to focus on the obstacle challenge. Regarding this second challenge, we completed the part about exiting the parking lot and began developing a program that recognizes traffic light colors and avoids them.
  
* **28/05/26:** Despite our upcoming exams, we’re still dedicating time to finishing and optimizing the program. We’re continuing to work on the obstacle course challenge, but now we’ve decided to also use the object recognition feature since HUSKYLENS was confusing the orange lines with the red traffic lights; once we fixed that, we continued developing the program. On the other hand, the R4 board with Wi-Fi/Bluetooth stopped working at the end of the day; we think the same thing might have happened as with the previous one, but we’re not sure. From now on, we’ll take greater precautions when handling the board, turning it on, turning it off, etc. 
  
* **29/05/26:** We started the day by setting up the new Arduino R4 Mini we bought the day before yesterday, just in case it broke again, and carried on with the obstacle course challenge. We’ve made good progress today as we came to school for a couple of hours this afternoon. As for the obstacle course programme, we’ve managed to get it to go round the right or left depending on the colour of the object. We’ve also decided we should fit a micro-servo to the camera so it can search for objects after passing those it has already seen; we’ve cut out the 3D structure we made for it to fit the servo and ensure it remains at the same height. Due to a lack of time and the number of exams we have, we haven’t had time to continue working on or test the robot much on the circuit; furthermore, we won’t be able to incorporate the latest modification (the servo on the HUSKYLENS support) into GitHub for the reasons mentioned above.

</details> 

<details>
<summary><b>💡 June 2026</b></summary>
<br>

* **02/06/26:** Regional competition day. We also asked the organizers if we could make a series of changes we’d come up with, since we felt that the current hardware wasn’t up to the task and we did not know if we were able to make such huge changes on the harware. The Arduino R4 MINIMA has limited programming language capabilities and overall capacity, which prevent us from properly developing the project; and the HC-SR04 and HC-SR04RC ultrasonic sensors give false readings when they aren’t measuring on a flat surface (they don’t allow us to measure at an angle). For this reason, we considered using, on the one hand, an Arduino Q or Raspberry Pi Pico 2 to replace the Arduino R4 MINIMA; and, on the other hand, laser sensors instead of the HC-SR04 and HC-SR04RC. They told us to draft an email to the WRO.

* **08/06/26:** We drafted and sent the email explaining the situation and the changes we want to make. 

* **11/06/26:** We received a reply; they’ll accept any changes we make. We looked into it and bought everything we need so it will arrive as soon as possible. 

* **15/06/26:** The 3D-designed chassis plate has bent under the weight of all the robot’s components. After evaluating possible modifications to the robot, the final decision was to redesign the plate in 3D to make it thicker so that it can adequately support the weight over time. 

* **16/06/26:** We’ve focused on one of the main modifications we’re going to make to the robot: replacing the ultrasonic sensors with laser sensors. Additionally, since we’ve been given the freedom to make as many modifications as we want, we came up with the idea of implementing a LiDAR for a new strategy in which the robot navigates by scanning with the LiDAR. With these two criteria in mind, we evaluated three options: 
  * TFmini-S.
  * TF Luna.
  * TFmini Plus. 
After evaluating all the options, we decided on the TFmini-S. The TF Luna isn’t powerful enough for this task; it has a shorter range and lower frequency, even though it’s cheaper and uses less power, and the TFmini Plus was too expensive, weighed too much, and consumed more power. 

* **17/06/26:** Today we focused on another major modification to the robot: replacing the ARDUINO R4 Minima board with a more powerful one, due to the limitations of the original board. Our two best options are the Arduino Q board and the Raspberry Pi Pico 2. The Arduino Q’s specifications are far superior to those of the Raspberry Pi Pico 2 (more power, built-in microprocessor and microcontroller, more RAM…), so we’re going to choose that one. 

* **18/06/26:** Since the idea of adding a battery holder to power various components—and thus prevent interference between them—yielded excellent results, we designed the holder using 3D printing because it is more durable than foam board. We also added stickers from the project’s various sponsors. 

* **23/06/26:** The distance sensors have arrived. We ran tests using a simple program to calibrate the measurements. We saved the data for the programming phase. 

* **24/06/26:** The Arduino Q board has arrived. When we tested it, we discovered that we’re going to face significant challenges when it comes to programming, since the microprocessor and the microcontroller—both integrated onto the same board—are programmed separately. Therefore, we’ll need to write two separate programs. After weighing the pros and cons of this approach, we’ve decided there isn’t enough time for that and that we’ll try the board we evaluated earlier, the Raspberry Pi Pico 2.
 
* **25/06/26:** The final decision regarding the board and its programming has been the Raspberry Pi Pico 2. We will program it in Visual Studio Code, a programming environment we are familiar with from various projects throughout the school year. To do this, we need to learn the Python language, but we believe we have time for that. 

* **26/06/26:** Since we don’t have the Raspberry Pi Pico 2 yet, we’ve assembled all the components on the new 3D base. In the meantime, we’re continuing to study Python so we’ll be ready when it’s time to program. 

* **29/06/26:** We’ve established a new strategy to tackle the challenge based on our experience in the regional competition:
  * First: The robot begins in a loop where the lights are flashing until the push button is pressed. When the button is pressed, the robot sweeps forward. If it doesn’t detect anything at a certain distance (we’ll figure that out later), the robot determines it’s in the free challenge; if it detects an obstacle at that distance, then it determines it’s in the obstacle challenge. 
  * Free Challenge: The robot moves backward until it detects the wall with the rear sensor. If this takes too long, it might be a good idea to add a color sensor to detect the line; this way, it could also determine whether the direction is clockwise or counterclockwise. Once it knows the direction and has detected the wall, it approaches the interior partition and circles it while maintaining a certain distance from the partition’s walls. At the same time, it counts the lines using the HUSKYLENS (it would be even easier with the color sensor). When the counter reaches a specific value, the robot stops in the quadrant from which it started.  
  * Obstacle Challenge: The robot exits the parking garage using the following maneuver: it moves backward to a certain distance from one of the garage walls, then turns completely to one side to exit. From there, whenever the HUSKYLENS detects an obstacle, it approaches it: if the obstacle is green, it goes around it on the left; if it’s red, on the right. The HUSKYLENS also continues counting the lines to stop the robot in the corresponding quadrant. 

* **30/06/26:** We’ve finally decided to incorporate a TCS34725 color sensor. We’ve used this sensor before in high school, which is why we chose it. We plan to wrap it in a layer of EVA foam to prevent confusion caused by light reflection and thus obtain more accurate readings. We’ll use this sensor to count the lines in both challenges.

</details> 

<details>
<summary><b>🔩 July 2026</b></summary>
<br>

* **02/07/26:** The Raspberry Pi Pico 2 arrived today. First, we installed the firmware so we could upload code from VS Code. Since this is a different board from the one we’ve been using, we’re going to start with the basics: getting the robot to follow the wall, measuring distances with the sensors... 

* **23/07/26:** Today we started with the basics: getting to know the board and seeing how it responds. The main problem is that we’re moving more slowly because we have to program in Python. 

* **24/07/26:** Today we continued conducting basic tests that will help us when we create our versions of the final program. After that, we made significant progress: we got the robot to follow the wall by controlling the distance between the robot and the wall at a constant speed. In other words, we’ve almost completed the obstacle-free challenge; we still need to figure out how to track the number of laps we complete and how to start from the starting zone. We’ve also noticed the difference between the ultrasonic sensors we had before and the laser sensors we have now; the laser sensors are much more precise, and they can also measure at an angle, unlike the ultrasonic ones. 

* **28/07/26:** We decided to finish the first test first (the challenge with no obstacles or parking). Once we made that decision, we continued thinking about how to count the laps we complete without using the HUSKYLENS, since counting the lines wasn’t very accurate. By late afternoon, we decided that a color sensor would be the best solution—one that detects the lines as the robot passes over them and distinguishes them by color. That way, the robot can keep track of how many laps it has completed and stop at the correct spot. We searched various online stores for color sensors that would meet our needs and have placed an order. In the meantime, we’re considering different strategies so that, from the starting point, the robot knows which direction to go and how to approach the wall in order to follow it and complete the three laps. Previously, we would back up until the side sensor could no longer detect the wall before the robot began to turn; this time, the robot will move backward, and depending on the color of the line it sees first, it will approach the wall in one way or another, depending on which direction it needs to turn. 

* **29/07/26:** The color sensor arrived today, and we ran some tests with it. To start with, we calibrated it, and now when it passes over the orange and blue lines, it tells us what color each one is. However, once we incorporated the color sensor into the program, we noticed that it doesn’t always detect them correctly or sometimes gets the colors mixed up. 

* **30/07/26:** As soon as we arrived at school, we picked up where we left off yesterday; we reviewed the part of the algorithm involving the color sensor and made some modifications to refine it. We ended the afternoon with our first perfect run—the robot is now able to complete three laps and stop in the correct zone regardless of the direction it takes (clockwise or counterclockwise). 

* **31/07/26:** Starting today, we’ll begin the second challenge (the obstacle challenge). We believe that this time we can do it right thanks to the hardware improvements with the light and laser sensors. Today, we only managed to get the robot to recognize that it’s in the obstacle challenge by measuring with the distance sensor and to exit the parking lot while orienting itself in the best way possible so it can easily see the obstacles.

</details>

<details>
<summary><b>⏳ August 2026</b></summary>
<br>

* **03/08/26:** We tested the program we hadn't tested the day before and realized that the right TOF400F can't detect the interior wall because it's so far away. After thinking about how we could solve this, we concluded that the best approach would be to use both TOF400F sensors (since we have one on each side) to navigate down the center of the hallway. Once we tested this, the same problem arose, so the only viable solution we found was the following: search for and avoid obstacles one by one, using the TF-mini-S to determine which one is closest in case the HUSKYLENS detects more than one, and aligning the chassis with the camera to center the obstacle. To do this, we decided to perform 90° scans with the front servo (HUSKYLENS + TF-mini-S), slowing down the robot’s speed to facilitate data collection. In addition, we took the opportunity to change our initial strategy for determining the orientation of the challenge; this time, we used the TOF400F sensors instead of the TF-mini-S, as we believe this will save us some time. 
Since we had slowed down the robot, we retested the free challenge to verify that there were no changes in its performance. During testing, we realized that the line counting was failing again, so we decided to use RGB values instead of brightness levels to identify the lines. This solved the problem. 
Before finishing, we decided to break down main.py into subprograms; since the program was too long and made it difficult to read, this way we can find what we're looking for more easily. 

* **04/08/26:** Today we started testing both challenges to get a clear idea of how we’re doing. During these tests, the robot had several issues recognizing which challenge it was on, and we believe the TF-mini-S is providing erroneous readings, so we decided to implement redundant checks using the side-mounted TOF400F sensors. This allowed us to resolve the issue, so we’re continuing with the open challenge. We’ve devised the following strategy, taking into account the three possible scenarios that could arise once the robot exits the parking lot:
  * 1. The robot does not see any obstacles; in this case, it should perform a 90° scan. If it sees nothing, it should perform an 180° scan (to expand the field of view), and if it still sees nothing, it should head toward where the TF-mini-S has detected a greater distance, thereby attempting to find the aisle.
  * 2. The robot detects an obstacle; in this case, the robot should move toward it until it is 12 cm away (which we have estimated to be sufficient for a successful dodge) and then dodge it on the correct side, using the corresponding side sensor to verify that the maneuver was performed correctly.
  * 3. The robot detects two obstacles; in this final case, we calculate the area of both objects (using the x and y data provided by HUSKYLENS), and once we know which one is closer, we implement the strategy from the previous case. In addition, if the robot detects another obstacle while avoiding one, we believe it should head directly toward it. We write the code. 

* **05/08/26:** We tested yesterday’s code, analyzing it step by step. Clearly, it isn’t working well for us—since it targets the first block it sees, it performs very abrupt scans until it dodges it, when it should lock onto the block and move toward it without scanning. We managed to fix this, which is a big improvement; however, we’re still running into problems. We decided to continue tomorrow. 

* **06/08/26:** The problem we identified yesterday is this: when the block is very close, the robot doesn’t have time to dodge it and ends up bumping into it. After brainstorming, we concluded that if we keep the block centered with HUSKYLENS at all times, we could track its location during the dodge and check the distance to it to avoid getting too close (if the distance is too low, the robot should move away); once it has dodged the block, the front servo would return to its forward position to continue with the challenge. We also decided to increase the distance at which the robot begins to avoid the block from 12 to 15 cm to allow for more room to maneuver. After making several changes to the program, it works better but not as well as we’d like; still, we decided to leave it as is for now. On another note, we’ve started researching the magnetometer (which we had previously purchased for the provincial and regional rounds but ultimately didn’t use), since we believe it could be quite useful for navigation purposes. 

* **11/08/26:** Since we were considering the idea of using the magnetometer, we realized we could use it for both the obstacle challenge and the free challenge. So, we started brainstorming ideas and decided to use it to align the robot with the direction of the street it was on. We would do this when the robot detected an orange line using the color sensor. When that happened, it would indicate that the robot had turned onto the next street and would therefore need to follow the new direction of that street. After testing it in both directions, we saw that everything was working correctly and decided to focus on the obstacle challenge. 

* **12/08/26:** We looked into the possibility of replacing the Husky Lens camera with one that had a wider field of view, but when we tried it, we realized it had too wide a field of view—it could see most of the objects in the classroom, but they appeared distorted, and the obstacles on the track looked too small. Therefore, we decided to keep the Husky Lens camera, even though it had a narrower field of view. 

* **13/08/26:** We tried completing the obstacle challenge without using the magnetometer, since we noticed it gives errors when we’re in a classroom with metal objects nearby. When trying to avoid three blocks, it successfully navigated the first two, but failed to clear the last one. We think this was because, after avoiding the second block, it ended up facing the outer wall, and when it finally turned, the camera didn’t detect the object and it drove right past it. Because of this, we’re going to try using the magnetometer again. 

* **14/08/26:** Today we revisited the idea of using the magnetometer in the obstacle course test and decided to have it scan the direction of each lane on the circuit at the start of the challenge. That way, if—while dodging an obstacle—it doesn’t find another one to avoid, as happened the previous day, it will align itself with the lane it’s in to continue searching for obstacles, just as we did in the free challenge.

<div align="center">
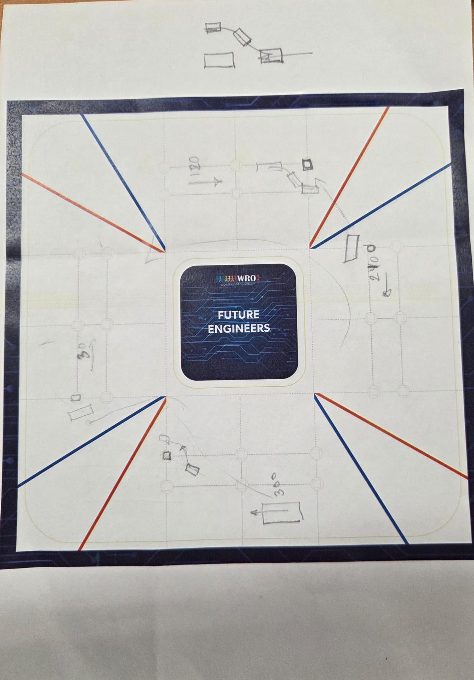
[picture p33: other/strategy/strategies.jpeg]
 
</div>

* **17/08/26:** Today, after testing the latest program we had, we realized that when the camera detected two obstacles and had to decide which one to pass first—since we told it that the one with the larger surface area should be passed first—the camera determined that the obstacle that should have been passed first actually had a smaller surface area than the one that should have been passed second, and it completely ignored the closer one. Therefore, we’ve decided that this time, instead of using surface area as a guide, we’ll use the Y-coordinate of the objects. Additionally, we think that after dodging an obstacle, the robot should perform an 180° scan, and while using the compass, it should also perform a slightly smaller scan—about 120°—to prevent it from missing any obstacles. We’ve also noticed that it gets quite close to the circuit walls. To fix this, we’re going to monitor the lateral distances using the TFmini-S. Finally, we’ve realized that when dodging a red object, it also gets quite close to it; therefore, we’re going to have the robot correct this by increasing the turning angle of the wheels so as not to displace the block.
  
* **18/08/26:** After testing yesterday’s program, we noticed that sometimes the robot keeps facing the outer wall, and when it scans, it fails to see the next block and skips over it. Therefore, since we couldn’t increase the angle any further, we decided to reduce the robot’s speed so that it doesn’t skip any obstacles while scanning. We’ve also noticed that when the robot moves backward, it only does so when approaching another robot instead of also using it to align itself; as a result, it passes some blocks incorrectly because it isn’t positioned properly, but we’ll leave this problem for tomorrow.
  
* **19/08/26:** We’ve identified several issues after running the latest program. The first one is that whenever it approaches an obstacle—regardless of whether it detects it as being too close or not—the robot backs up. This is because it moves toward the block too quickly, and when it stops, it ends up too close to the obstacle and ultimately has to back up. However, it doesn’t back up far enough, so it ends up avoiding some blocks on the wrong side. We’re going to modify it so that the robot backs up until it’s about 18 cm from the block and can avoid it perfectly, after a reading from the TFmini-S while the HuskyLens camera screen has the block centered. While testing the modified program, we’ve noticed that sometimes, when trying to align itself with the direction of the street and not seeing anything, it heads toward the outer wall and pushes against it.
  
* **20/08/26:** We realized that the problem we encountered yesterday—where the robot was moving toward the outer wall and pushing against it, is due to the fact that when it exits a block, we’ve programmed it to move slowly until it’s completely out of the block, while the compass instructs the robot to turn right. As it approaches the wall, it tries to move away in the opposite direction, which is why the robot gets stuck. So we’re going to make it so that when the course deviation is too large—exceeding 45°—the robot reduces its speed even more than it would for a smaller deviation. And to prevent it from getting stuck, we’ll have the robot turn while backing up to correct its position when it’s too close to the wall and get back on course. We’ve also noticed that sometimes, when clearing an obstacle with the left TOF400F, it takes too long to realize that it has already cleared it. So now we’re going to use the TFmini-S to handle this.
  
* **21/08/26:** We spent the day refining our documentation on GitHub to try to achieve the highest score on each of the competition’s documentation requirements.
  
* **24/08/26:** We’ve realized something. After running the program and while it was following the course, we noticed that our robot’s wheels were slipping on the track, causing the robot to drift slightly as it moved along the path. We believe this is because the back of the robot carries significantly more weight than the front. That’s why we’ve decided the best option would be to add more weight to the front using lead so the wheels don’t slip. We’ve also noticed that when trying to avoid a block—and while it uses the TFmini-S to determine whether it has passed it or not—sometimes it does so correctly, but other times it ends up too far away. We could solve this by avoiding the blocks based on time.

* **25/08/26:** By placing the lead weight at the front, we have managed to stop the robot’s front wheels from skidding. However, we have noticed that we are still experiencing the same problems we had some time ago. Firstly, when approaching a block, it continues to reverse, even when it is not necessary. Secondly, when passing a block, sometimes it does so correctly and other times it carries on forwards, knocking the obstacle over. We believe this is because, when it is about to avoid an object, the TFmini-S servo and the Husky Lens should instantly move to 90° on the corresponding side once it has passed the obstacle, but it does not do so. To solve both problems, we are going to make it turn right first, move straight ahead for a short while, turn left and then move straight ahead again. The third problem we have observed is that when it aligns with a pillar, the direction straightens out gradually, and this costs us quite a bit of time. That is why we have decided it should continue to do so, but at a slightly faster pace so as not to lose so much time. Finally, we’ve carried out the necessary calculations to determine: the torque, the revolutions per minute and the maximum speed the robot reaches.

* **26/08/26:** Today we carried out a test with three red blocks in a row. At the second obstacle, as soon as it had finished going round it and just before checking whether it had passed it, the robot performed a sweep to check for further blocks, rather than doing so without moving the servo. As a result, the robot detected this second obstacle again, avoided it once more, and has now moved on to the third block. The solution to this problem is that, instead of simply using the Husky Lens to check for an obstacle, we’ll use the TFmini-S to determine whether it’s more than 30 cm away, to ensure it isn’t avoiding the same obstacle again. Furthermore, we’ve noticed that sometimes, during the initial scan, it detects the car park wall and mistakes it for a block. So we’ve added a small straight-line movement to prevent this confusion.

* **27/08/26:** We started by focusing on the problem of the robot getting too close to the wall. What we’ve done is make it check the distance to the wall on the left and on the right; if either is less than 30 cm, it means it’s close to a wall and must therefore correct its course by adding a value to the compass heading. However, we’ve found that when implementing yesterday’s modification, we’ve uncovered a new problem. After finishing going round the obstacle, if it spots an object before checking whether it has already passed it or not, it heads straight for it. The problem is that sometimes it spots an obstacle in the distance and ignores the one that is closer. Therefore, we are going to programme it so that, upon finishing going round the block, it checks whether there is an object in front of it, but by scanning 30° to each side. After sorting out this problem, we’ve spotted another one. We’ve now realised that it no longer backs up if it’s very close to a block in order to avoid it more effectively. Instead, it ploughs straight through it and ends up facing the same object again. We’ve now programmed it to back up when the object is at a distance of 25 cm or less. But we’ll leave that to sort out tomorrow.

* **28/08/26:** Today we have once again focused on improving our documentation.

* **31/08/26:** Let’s pick up where we left off the other day. We’ve now identified why the robot was previously knocking the block over: it’s because we’ve programmed it to start dodging when the object is 15 cm away, but what actually happens is that it starts dodging when it’s 5 cm away, which is why it ends up knocking it over. This is because, immediately after taking the reading, the camera has to be repositioned, the LED switched on and other tasks carried out within the same loop; consequently, until it has completed all of these, it does not detect that it has reached the block or start to swerve. As a solution, we’ve programmed it to check whether it has reached the block immediately after sending the reading, and only then carry out everything else. And now it only reverses in extreme cases where it is 7 cm or less away.

* **01/09/26:** We managed to get our robot to complete three full laps of the circuit in the obstacle challenge, starting from the parking area, but we were unable to return and park in the parking area, and we had to remove the parking area before completing the first lap as we spotted a problem. Due to the quality of the Husky Lens, it recognises the parking area as a red block. We have therefore decided to change our strategy. We will now start the obstacle challenge without the parking area.

* **02/09/26:** Hemos empezado a lanzar ideas para ver cómo resolvemos la decisión inicial, la que hace que sepa si está en reto libre o con obstáculos y si está girando a sentido horario o antihorario. Hemos llegado a la conclusión de que el robot debería ir marcha atrás y, tras ello, que la Husky Lens mire hacia la izquierda y hacia la derecha para ver si hay bloques. Si los encuentra, para saber hacia qué sentido está, miraríamos si la coordenada X del objeto es mayor de 160, giraría en sentido horario, y si por lo contrario es menor de 160, giraría en sentido antihorario. Si aun así no los ve, tiene que ir hacia delante hasta sobrepasar la esquina y hacer la primera curva. Si no ve ningún bloque significa que está en el reto libre y, si por lo contrario ve alguno, está en el reto con obstáculos.

* **03/09/26:** Today we’ve come up with an idea regarding the robot’s speed, as the motor isn’t running as fast as we’d like. The idea is to fit a larger gear than the one we currently have. We’d fit a 50-tooth gear so that the robot can complete the challenges more quickly. We’ve also decided to remove the edges from our base so that it doesn’t knock over any blocks or hit the walls, although we’re not sure when we’ll implement this change. Also, whilst running the programme for the obstacle challenge, we decided to remove the feature where it checks for walls every now and then to avoid collisions, as it sometimes gets confused by this. Finally, we’ve noticed that in the latest tests our robot confuses the orange lines with red blocks, but we’ll look into this further tomorrow.

* **04/09/26:** As we mentioned yesterday, our camera was mistaking the orange lines on the circuit for red blocks and ended up crashing into the wall. Well, as soon as we arrived today, we tried to track down the error and discovered that it is due to the lighting in the classroom where we are working; when we focused on the areas where it was getting confused, using the torches on our phones, it worked perfectly. However, we are still going to try to fix the problem by making smaller sweeps around the bends so that it does not detect the orange line as a red block.

</details>

### <span id="seccion-mecanica"></span>4. 🛠️ Mechanical Design
This section is dedicated to the robot’s mechanical components: the list of parts used in its construction and the 3D-printed parts we designed and printed.

<details>
<summary><b> 4.1 Old components and 3D designs</b></summary>
<br>
Here is a also a list of all components we used to use before our modifications; including an image, their specific function in the robot, and a purchase link: 

| Component | Quantity | Image | Function | Purchase link |
| :---: | :---: | :---: | :---: | :---: |
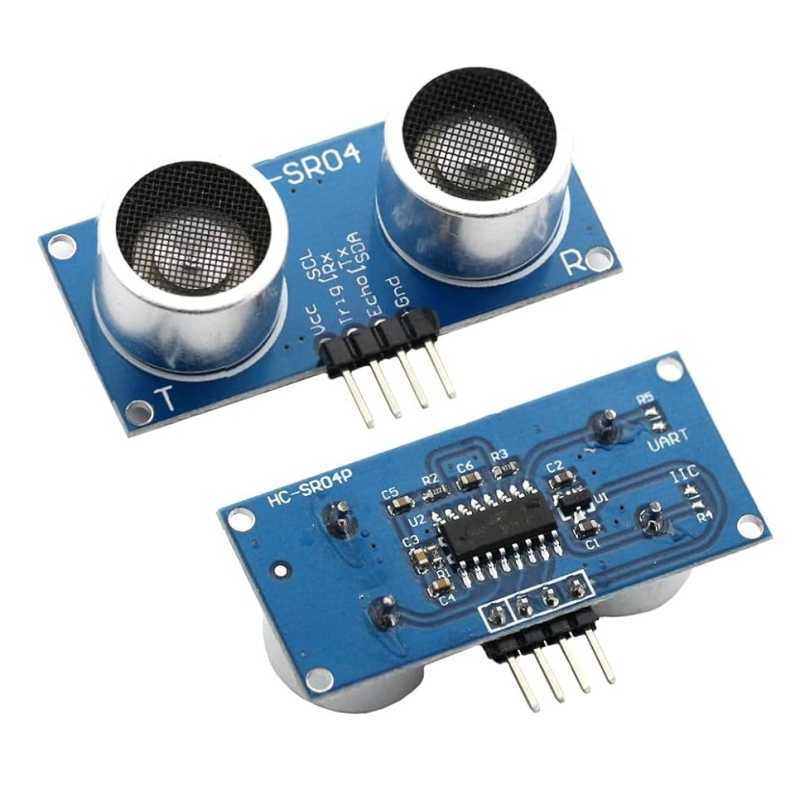
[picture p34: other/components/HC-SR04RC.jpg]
| HC-SR04RC | 2 |  | Measure distances | <a href="https://www.tiendatec.es/maker-zone/modulos/2785-sensor-ultrasonico-hc-sr04rc-con-chip-rcwl-9616-gpio-uart-i2c-y-1-wire.html"> 🛒 Shop</a> |
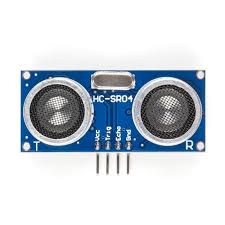
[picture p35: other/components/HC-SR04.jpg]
| HC-SR04 | 2 |  | Measure distances | <a href="https://es.aliexpress.com/item/1005010373195248.html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"> 🛒 Shop</a> |
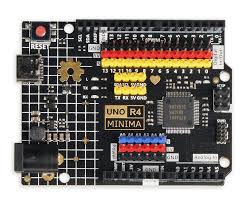
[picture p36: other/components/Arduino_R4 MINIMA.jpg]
| Arduino R4 MINIMA | 1 |  | Robot controller | <a href="https://www.amazon.es/Arduino-UNO-Minima-ABX00080-Connector/dp/B0C78K4CD4"> 🛒 Shop</a> |
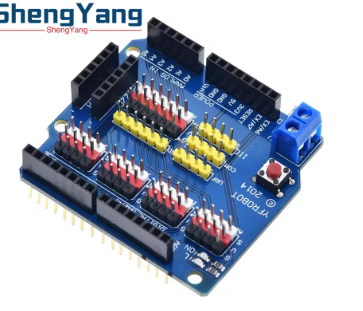
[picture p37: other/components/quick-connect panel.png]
| Quick-connect panel | 1 |  | It allows us to connect all the sensors and servos to the Arduino thanks to all the pins it has |  <a href="https://es.aliexpress.com/item/1005007370390696.html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)"> 🛒 Shop</a> |
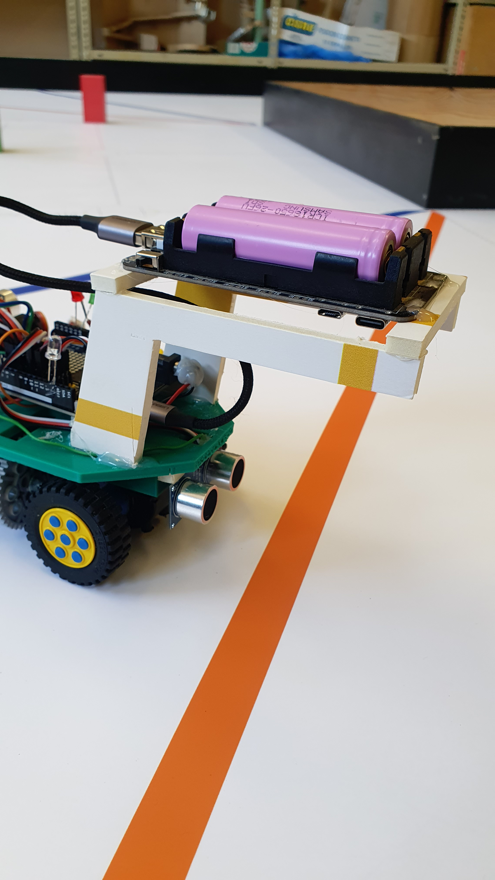
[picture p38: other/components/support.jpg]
| Battery support | 1 |  | Is the support of the second battery | We made it in class using a kind of cardboard and hot glue|
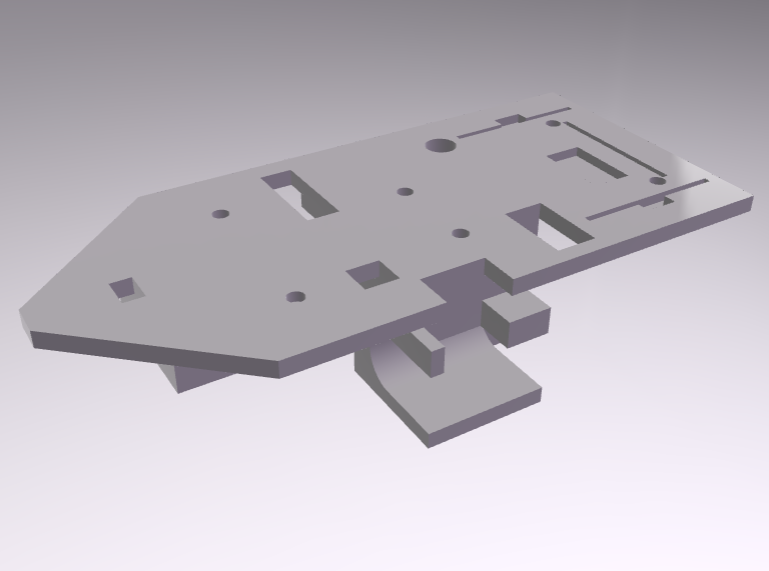
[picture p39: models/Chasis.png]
| Chasis in 3D | 1 |  | Skeleton of the robot | [`📥Download`](models/CHASSIS.stl) |

</details>

<details>
<summary><b> 4.2 Current components List </b></summary>
<br>
Here is a list of all components we used, including an image, their specific function in the robot, and a purchase link: 

| Component | Quantity | Preview | Main Function | Purchase link |
| :---: | :---: | :---: | :---: | :---: |
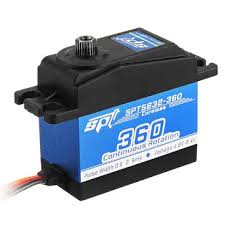
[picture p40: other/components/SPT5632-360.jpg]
| SPT5632-360 | 1 |  | Robot mobility | <a href="https://de.banggood.com/SPT-Servo-SPT5632-360-Coreless-Digital-Servo-Metal-Gear-Lager-Torque-Linear-Change-For-RC-Robot-p-1418818.html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"> 🛒 Shop</a> |
| MS18 | 1 |  | Robot direction system | <a href="https://es.aliexpress.com/item/1005012158832496.html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"> 🛒 Shop</a> |
| TFmini-S | 1 |  | Measure distances | <a href="https://es.aliexpress.com/item/1005008667948116.html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"> 🛒 Shop</a> |
| T0F400F | 2 |  | Measure distances | <a href="https://es.aliexpress.com/item/1005006223800307.html"> 🛒 Shop</a> |
| LED | 2 |  | Checkpoints | <a href="https://es.aliexpress.com/item/1005009812533874.html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"> 🛒 Shop</a> |
| HUSKYLENS | 1 |  | Object detection | <a href="https://www.amazon.es/HUSKYLENS-inteligente-Seguimiento-Reconocimiento-etiquetas/dp/B089GLJHZD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"> 🛒 Shop</a> |
| Raspberry pi pico 2 rp2350 | 1 |  | Robot controller | <a href="https://www.raspberrypi.com/products/raspberry-pi-pico-2/"> 🛒 Shop</a> |
| KS3017 Keyestudio Raspberry Pico IO Shield | 1 |  | Conexions | <a href="https://es.aliexpress.com/item/1005003882137188.html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"> 🛒 Shop</a> |
| 10 DOF IMU sensor (L3GD20 - gyroscope) | 1 |  | Robot orientation | <a href="https://es.aliexpress.com/item/1005012492343486.html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"> 🛒 Shop</a> |
| TCS34725 RGB sensor | 1 |  | Lines detection | <a href="https://es.aliexpress.com/item/1005007392355136.html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"> 🛒 Shop</a> |
| Rocker Switch | 1 |  | Power on and off robot switch | <a href="https://es.aliexpress.com/item/1005008525408190.html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"> 🛒 Shop</a> |
| Pull down button | 1 |  | Starter robot program button | <a href="https://es.aliexpress.com/i/1005002576288170.html"> 🛒 Shop</a> |
| Samsung battery 2600mAh | 4 |  | Batteries | <a href="https://bateriasonline.com/es/baterias-litio-recargable/bateria-litio-samsung-icr-18650-26j-2600mah-samsung-baterias-litio-recargable.html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"> 🛒 Shop</a> |
| Lego wheels 30,4x14 | 2 |  | Directional wheels | <a href="https://www.toypro.com/es/product/33208/rueda-18-mm-d-x-14-mm-con-agujero-para-pasador-pernos-falsos-y-radios-poco-profundos-con-llanta-negra-30-4-x-14-banda-de-roda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"> 🛒 Shop</a> |
| Lego wheels 13x24 | 2 |  | Drive wheels | <a href="https://www.steinpalast.eu/en/1-x-lego-brick-light-gray-wheel-30mm-d.-x-13mm-13-x-24-model-team-with-black-tire-13-x-24-model-team-2695-4141535-2696-269626-2695c01"> 🛒 Shop</a> |
| Servo arm | 1 |  | Servo direction arm | <a href="https://es.aliexpress.com/item/1005012158832496.html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"> 🛒 Shop</a> |
| Gear teeth Lego 4285634 | 1 |  | Gear teeth transmission | <a href="https://www.electricbricks.com/lego-piezas-lego-technic,-engranaje-gris-claro-azulado-engranaje-dientes-p-425.html"> 🛒 Shop</a>|
| Lego structure piece 4495931 | 3 |  | Maintain direction structure | <a href="https://www.toypro.com/es/product/3937/liftarm-1-x-7-grueso/gris-azulado-oscuro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"> 🛒 Shop</a>  |
| Lego structure piece 4210686 | 3 |  | Connect directional wheels and connect them with the structure | <a href="https://es.aliexpress.com/item/1005011819503855.html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"> 🛒 Shop</a> |
| Lego piece 4514554 (3 modules) | 3 |  | Connect the directional | <a href="https://www.toypro.com/es/product/1776/technic-pin-largo-sin-estrias-de-friccion-longitudinales/tan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"> 🛒 Shop</a> |
| Lego piece 4514553 (3 modules) | 4 |  | Connect the directional structure and connect it with chassis | <a href="https://www.toypro.com/es/product/2247/technic-pin-largo-con-estrias-de-friccion-longitudinales/azul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"> 🛒 Shop</a> |
| Lego piece 4211807 (2 modules) | 2 |  | Connect the directional structure | <a href="https://www.toypro.com/es/product/756/technic-pin-sin-estrias-de-friccion-longitudinales/gris-azulado-claro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"> 🛒 Shop</a> |
| Lego piece 4495931 (2 modules) | 1 |  | Connect directional structure | <a href="https://www.toypro.com/es/product/1152/technic-pasador-de-eje-sin-estrias-de-friccion-longitudinalmente/tan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"> 🛒 Shop</a> |
| Lego piece 4560175 | 1 |  | Connect directional structure | <a href="https://www.toypro.com/es/product/2210/technic-pasador-largo-con-estrias-de-friccion-longitudinales-y-orificio-central-para-el-pasador/gris-azulado-claro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"> 🛒 Shop</a> |
| Lego piece 4107767 | 2 |  | Connect directional wheels with directional structure | <a href="https://www.toypro.com/es/product/577/eje-y-conector-de-pin-n-6-90/negro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"> 🛒 Shop</a> |
| Lego piece 4107085 | 2 |  | Connect directional structure | <a href="https://www.toypro.com/es/product/152/eje-y-conector-de-pin-n-1/negro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"> 🛒 Shop</a> |
| LM7805CT | 2 |  | Supply energy to huskylens directly of the batteries | <a href="https://richelectronics.co.uk/product/motorola-mc7805ct-3-terminal-positive-voltage-regulator-5-pieces-oma77"> 🛒 Shop</a> |
| Electrolytic condenser 0,1 microfarad | 1 |  | (maker recommendation) | <a href="https://www.ebay.com/itm/202550513396"> 🛒 Shop</a> |
| Electrolytic condenser 0,33 microfarad | 1 |  | (maker recommendation) | <a href="https://www.tme.eu/en/details/uvy2dr33med/tht-electrolytic-capacitors/nichicon/"> 🛒 Shop </a> |
| Circuit board | 1 |  | Connect huskylens with the LM7805CT and then with batteries | <a href="https://www.pccomponentes.com/goobay-regleta-para-conexion-de-cables-electricos-de-10a-10mm-blanco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"> 🛒 Shop</a> |
| Differential QBX01 1:12 | 1 |  | It allows the drive wheels to rotate at different speeds on curves, preventing slippage | <a href="https://es.aliexpress.com/item/1005005425198232.html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"> 🛒 Shop</a> |
| Power Expansion Board Module | 2 |   | It's a type of power bank where we've used the same Samsung batteries | <a href="https://es.aliexpress.com/item/1005001829484812.html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"> 🛒 Shop</a> |
| Micro Servo MG90S | 1 |  | Allow the camera to move and have a wider field of view | <a href="https://www.hta3d.com/es/microservo-mg90s-180-de-posicionamiento-engranajes-metalicos"> 🛒 Shop</a> |"> Camera servo link </a> |
| Heatsink | 1 |  | Prevent the current regulator from overheating | <a href="https://www.amazon.es/WayinTop-Disipador-Aislamiento-Transistor-Casquillos/dp/B081GS15N6"> 🛒 Shop</a> |
| USB-Kabel | 1 |  | It makes it easy to connect the robot to the computer to upload programmes or view the terminal when we’re carrying out tests, in a simple and convenient way that prevents the Raspberry Pi’s connector from breaking. | <a href="https://es.aliexpress.com/item/1005007053499029.html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"> 🛒 Shop</a> |
| Counterweight | 2 |  | We use it to adjust and balance the robot’s weight, as the rear is quite heavy due to the spoiler housing the batteries, which is why we place it at the front. In this case, there are two of them, and each one weighs 40 grams | <a href="https://selectauto.es/consumibles-para-ruedas/6175-contrapesos-para-llantas-de-aleacion-40gx50-uds-marca-seltech-5949128213693.html"> 🛒 Shop</a> |

</details>

<details>
<summary><b> 4.3 Current 3D Designs </b></summary>
<br>

These are the 3D designs we have created, which include: a custom-made chassis for all components, a gear to connect the differential to the 360-degree servo, a rear wheel adapter to connect the differential shaft to the wheels and a mount for the HUSKYLENS module:

| Component | Quantity | Image | Function | File link |
| :---: | :---: | :---: | :---: | :---: |
| Chasis in 3D | 1 |  | Skeleton of the robot | [`📥Download`](models/CHASIS_modificado_2.stl) |
| Battery support 1 | 2 |  | Support batteries | [`📥Download`](models/soportebateria1.stl) |
| Battery support 2 | 1 |  | Support batteries | [`📥Download`](models/soportebateria2.stl) |
| Switch support | 1 |  | Support the switch | [`📥Download`](models/SOPORTE_INTERRUPTOR.stl) |
| Adapter wheels in 3D | 2 |  | Connect the wheels to the differential | [`📥Download`](models/wheel%20adapter.stl) |
| Adapter gear in 3D | 1 |  | Gearing with 360º servo gear | [`📥Download`](models/GEAR_ADAPTER.stl) |
| Magnetometer mast | 1 |  | Support the magnetometer | [`📥Download`](models/SOPORTE_10-DOF.stl) |

</details>

### 5. 🪛 Mobility design
This section includes an overview of the robot's components, speed and torque calculations, and the steering, motor and transmission systems.

<details>
<summary><b>5.1 Old Mobility design</b></summary>
<br>
 
Generally speaking, the robot has:

* An Arduino R4 board (chosen based on previous experience programming it) 
* Four HC-SR04 sensors (one at the front, one at the rear, and two on the sides, one on each side): the front and side sensors are mounted on top of the chassis on a small piece of foam board to...; the rear sensor is mounted underneath the chassis due to space constraints at the rear top of the chassis. The triggers for the four sensors are soldered to the same pin to save pins on the Arduino board, in case more components need to be connected. 
* Four Samsung batteries... two of which power the Arduino board directly... 
* A 360-degree servo that functions as a servo motor. 
* A transmission system made with LEGO gears and one made with 3D-printed parts that runs from the servo motor to the mechanical differential. 
* A mechanical differential equipped with two adapters for 3D printers to ensure a better fit on the wheels. 
* Four LEGO wheels (two larger and two smaller: the specific models are listed in the parts list). 
* Un sistema de dirección de LEGO (piezas usadas en la lista de componentes). 
* An 180-degree servo to move the LEGO steering system via an arm attached to a string that runs to the steering system. 
* A HUSKYLENS module for detecting obstacles. 
* A foam board frame for holding a couple of batteries. 
* A switch to turn on the robot. 
* A button to start the program.

#### Steering system 
The steering system used consists of:  

* A system made from LEGO bricks from our Technology class, because it’s easy to assemble and disassemble and can be put together fairly quickly in case modifications are needed, featuring two LEGO wheels that are smaller than the rear ones.  
* An 180-degree servo, since it’s easy to program and a larger turning angle wasn’t necessary given the system we built.  
* A servo arm with a string, to connect the LEGO steering system to the servo.

<table>
  <tr>
    <td align="center" width="33%">
      
    </td>
    <td align="center" width="33%">
      
    </td>
    <td align="center" width="33%">
      
    </td>
  </tr>
</table>

If this steering turned too far in one direction, it would jam and could break. To prevent this, we adjusted the values using the steering servo calibration program so that this wouldn’t happen.  

<div align="center"><table>
  <tr>
    <td align="center" width="50%">
      <b>Micro servo 180</b><br>
      
    </td>
    <td align="left" width="50%">
      <ul>
        <li>A:32mm</li>
        <li>B:23mm</li>
        <li>C:28,5mm</li>
        <li>D:12mm</li>
        <li>E:32mm</li>
        <li>F:19mm</li>
        <li>Speed:0,1sec</li>
        <li>Torque:2,5kg-cm</li>
        <li>Weight:14,7g</li>
        <li>Voltage:4,8-6V</li>
      </ul>
    </td>
  </tr>
</table></div>

#### Drive system
The motor system used consists of: 

* A 360-degree continuous-rotation servo (model listed in the parts list). 
* A gear system to transmit motion from the servo motor to the mechanical differential, consisting of a 40-tooth LEGO gear and a 13-tooth gear made with a 3D printer. The gear ratio is 12:30. 
* A mechanical differential. The differential was purchased from AliExpress based on an idea from a previous project in our Technology classroom. 
* Two 3D-printed adapters that connect the differential shafts to the LEGO wheels. 
* Two LEGO wheels larger than those in the steering system. 

The first 360-degree continuous rotation servo we installed caused smoothness issues when the robot moved, leading us to believe the problems were software-related; however, when it was replaced with another one we had in our classroom, the issues did not recur. 

The mechanical differential was a bit stiff to turn when it arrived. To make it turn more smoothly, we lubricated it with oil and turned it using a drill. 

The rear wheels are larger than the front wheels because the front wheels had to cover the height of the mechanical differential on their own; the front wheels already accounted for the height of the LEGO steering system.

#### Chassis design

The chassis has evolved based on the need to add or remove components, and depending on what was most practical for meeting the challenges. 

Initially, we used a sheet of foam board that was in the classroom, onto which we gradually added all the components. To attach the components, we used hot glue (because it has good adhesive properties, allows us to make modifications easily, and doesn’t damage the components). In fact, the first prototype was tested with a foam board base. 

The front is cut into a pointed shape to prevent it from coming into contact with any of the interior partition walls or those of the parking garage during the obstacle phase. 

<div align="center"><table>
  <tr>
    <td align="center" width="33%">
      
    </td>
    <td align="center" width="33%">
      
    </td>
    <td align="center" width="33%">
      
    </td>
  </tr>
</table></div>

After confirming that this was the final base, we designed the chassis in 3D, printed it, and transferred the components from one base to the other. Although we thought this change might cause problems once everything was already assembled, there were none. 

<p align="center"></p>

An important consideration regarding the robot’s balance was to place the heaviest components (the Arduino board, the batteries, the 360-degree servo) in the center of the chassis, maintaining a low and centralized center of mass. The batteries that directly power the 360-degree servo (explained in detail below) are located in a separate structure, as this was a last-minute modification.

The robot remained in that state for a time until we encountered several problems and some broken circuit boards, which forced us to build a mount for a second battery, as recommended in the instructions.

<div align="center"><table>
  <tr>
    <td align="center" width="33%">
      
    </td>
  </tr>
</table></div>

Finally, the servo we fitted to the HUSKYLENS to make the camera rotate was causing problems, so we decided to remove it and build a 3D structure to hold it in place, allowing us to view objects and lines from a better angle without needing a servo. We also positioned the camera so that it was pointing slightly downwards, to avoid confusion with other objects and colours in the surroundings.

</details>

<details>
<summary><b>5.2 Current Mobility design</b></summary>
<br>

Generally speaking, the robot has:

* Microcontroller: Raspberry Pi Pico 2 board on a KS3017 shield.
* Motor system: SPT5632-360 servo.
* Drivetrain: mechanical differential, gear system, differential-to-wheel adapters, and four LEGO wheels, two of which are larger than the others.
* Steering system: LEGO brick system, 180-degree micro servo, and a servo arm with a string to connect the micro servo to the steering system.
* Camera: HUSKYLENS module.
* Distance sensors: one TFmini-S sensor, two TOF400F sensors.
* Gyroscope: L3GD20 gyroscope.
* Color sensors: TCS34725 RGB sensor.
* Power supply: four Samsung ICR18650-26FU batteries, arranged in pairs across two battery expansion modules.
* Other components: a pushbutton to start the robot, a switch to turn on the batteries, a micro servo to rotate the HUSKYLENS and the TFmini-S sensor, red and green LEDs to provide hardware feedback on the program, and a heat sink connected to a current regulator for the HUSKYLENS module with two electrolytic capacitors.

All of the components mentioned above are explained in greater detail below.

#### Steering system 
The steering system used consists of:  

* A system made from LEGO bricks from our Technology class, because it’s easy to assemble and disassemble and can be put together fairly quickly in case modifications are needed, featuring two LEGO wheels that are smaller than the rear ones because they had to account for the height of the steering system.  
* An 180-degree servo, since it’s easy to program and a larger turning angle wasn’t necessary given the system we built.  
* A servo arm with a string, to connect the LEGO steering system to the servo.

<table>
  <tr>
    <td align="center" width="33%">
      
    </td>
    <td align="center" width="33%">
      
    </td>
    <td align="center" width="33%">
      
    </td>
  </tr>
</table>

If this steering turned too far in one direction, it would jam and could break. To prevent this, we adjusted the values using the steering servo calibration program so that this wouldn’t happen.  

<div align="center"><table>
  <tr>
    <td align="center" width="50%">
      <b>Micro servo 180</b><br>
      
    </td>
    <td align="left" width="50%">
      <ul>
        <li>A:32mm</li>
        <li>B:23mm</li>
        <li>C:28,5mm</li>
        <li>D:12mm</li>
        <li>E:32mm</li>
        <li>F:19mm</li>
        <li>Speed:0,1sec</li>
        <li>Torque:2,5kg-cm</li>
        <li>Weight:14,7g</li>
        <li>Voltage:4,8-6V</li>
      </ul>
    </td>
  </tr>
</table></div>

#### Drive system
We used an SPT5632-360 servo motor because we already had experience programming it, and it has enough power to achieve the torque and speed required for both challenges.

<div align="center"><table>
  <tr>
    <td align="center" width="50%">
      
    </td>
    <td align="left" width="50%">
     <ul> 
      <li>Type: 360° continuous rotation digital servo</li>
      <li>Voltage: 4.8–8.4 V</li>
      <li>Speed: 56–88 rpm</li>
      <li>Rated current: 1.5 A</li>
      <li>Maximum current: 2.5 A</li>
      <li>Gears: Metal</li>
      <li>Motor: Coreless</li>
      <li>Weight: ≈58 g</li>
      <li>Dimensions: 40.5 × 20 × 37.5 mm</li>
     </ul>
    </td>
  </tr>
</table></div>

The first 360-degree continuous-rotation servo we installed caused problems with smooth motion when the robot moved, which led us to believe the issues were software-related; however, when it was replaced with another one we had in class, the problems did not recur.

#### Drivetrain

The drivetrain consists of:

* A gear system designed to transmit motion from the servomotor to the mechanical differential, consisting of a 40-tooth LEGO gear and a 13-tooth gear produced via 3D printing. The gear ratio is 12/30.
* A mechanical differential. The differential was purchased from AliExpress, inspired by an old project we did in our technology classroom.
* Two adapters made with a 3D printer that connect the differential shafts to the LEGO wheels.
* Two LEGO wheels that are larger than those in the steering system because they had to account for the height of the mechanical differential on their own.

<table>
  <tr>
    <td align="center" width="33%">
      
    </td>
    <td align="center" width="33%">
      
    </td>
    <td align="center" width="33%">
      
    </td>
  </tr>
</table>

The mechanical differential was somewhat stiff when turning. To make it turn more smoothly, we lubricated it with oil and turned it using a drill.

In addition, we have recalculated the maximum speed, the revolutions per second of the different axles, the force and torque. The traction servomotor we are using has been discontinued and we cannot find its torque or rotational speed specifications. We have derived the servo’s rotational speed from the robot’s linear speed, so we have worked the calculations ‘backwards’ to arrive at this figure. We did the same with the torque: we measured the robot’s force using a dynamometer; we ran the motor at full power, had it pull on a dynamometer, and pressed the wheels indirectly against the floor until they began to slip. The maximum pull we recorded was 4 N. As there are two drive wheels, this gives us a thrust of 2 N per wheel.
<br>
</br>
Torque of each wheel:
<br>
</br>
F= 2 N
<br>
</br>
r= 21,5 mm = 0,0212 m
<br>
</br>
T= 2 N · 0,0212 m = 0,0424 N·m
<br>
</br>
<table>
  <tr>
    <td align="center" width="50%">
      
    </td>
    <td align="center" width="50%">
      
    </td> 
  </tr>
</table>

#### Chassis design

The chassis has evolved based on the need to add or remove components, and depending on what was most practical for meeting the challenges. 

Initially, we used a sheet of foam board that was in the classroom, onto which we gradually added all the components. To attach the components, we used hot glue (because it has good adhesive properties, allows us to make modifications easily, and doesn’t damage the components). In fact, the first prototype was tested with a foam board base. 

The front is cut into a pointed shape to prevent it from coming into contact with any of the interior partition walls or those of the parking garage during the obstacle phase. 

<div align="center"><table>
  <tr>
    <td align="center" width="33%">
      
    </td>
    <td align="center" width="33%">
      
    </td>
    <td align="center" width="33%">
      
    </td>
  </tr>
</table></div>

After confirming that this was the final base, we designed the chassis in 3D, printed it, and transferred the components from one base to the other. Although we thought this change might cause problems once everything was already assembled, there were none. 

<p align="center"></p>

The robot remained in this configuration for a while until we encountered several issues and broken circuit boards, which forced us to build a mount for a second battery as recommended in the instructions. Initially, it was made of foam board since it was a last-minute modification, but it was later 3D-designed to ensure a more durable and reliable material over time.

<div align="center"><table>
  <tr>
    <td align="center" width="33%">
      
    </td>
    <td align="center" width="33%">
      
    </td>
    <td align="center" width="33%">
      
    </td>
  </tr>
</table></div>

Finally, after the regional competition, the chassis had bent under the weight of the components, so we designed a new one with minor modifications—thicker so it could easily support them over time.

An important consideration regarding the robot’s balance was to place the heaviest components—the Raspberry Pi Pico 2 board with its shield, the SPT5632-360 servo, and a pair of batteries with their expansion module—in the center of the chassis, ensuring a low and centralized center of mass.

However, the addition of the other two batteries—a last-minute modification—forced us to build a special structure for them at the rear of the robot. Over time, it became apparent that when accelerating, the robot would sometimes skid due to an overload at the rear. To compensate for this extra weight, lead plates were added to the front of the robot.

<div align="center"><table>
  <tr>
    <td align="center" width="33%">
      
    </td>
    <td align="center" width="33%">
      
    </td>
    <td align="center" width="33%">
      
    </td>
  </tr>
</table></div>

The chassis was always designed to provide a stable and reliable foundation on which to mount the components, avoid unnecessary wiring, provide specific spaces for certain components, save space, and keep the robot compact throughout its journey through the challenges.

</details>

### 6. ⚡ Power and Sensor Architecture 

This section includes the robot's power supply, the wiring diagram created in Cirkit Designer, everything related to the sensors that provide information to the board, and the reasoning behind the sensor layout.

<details>
<summary><b>6.1 Old Power and Sensor Architecture</b></summary>
<br>

#### Power Supply 
The robot uses four Samsung ICR18650-26FU batteries as its power source. Two batteries power the Arduino R4 board, and the other two directly power the 360-degree servo motor. This prevents interference with the servo, allowing the robot to move smoothly.  

An energy estimate was calculated for all components to determine the appropriate batteries:  

* HUSKYLENS module: 230–420 mA.  
* Arduino R4 Minima board: 100 mA.  
* HC-SR04 sensors: 15 mA  
* 180-degree microservo: 200 mA  
* 360-degree continuous rotation servo: 700 mA  
* Total: 1215 mA 

Theoretically, this is the robot’s power consumption. However, after measuring the robot’s actual power consumption, it was 500 mA. Therefore, with two batteries (2600 mA), we have enough power for 5 hours. These were the initial calculations since we were only going to use two batteries. Finally, after verifying that using two batteries connected directly to the 360-degree servo and the HUSKYLENS module works as intended, we will now connect four batteries (5200 mA), which theoretically gives us:  

* Battery life for the 360° servo and the HUSKYLENS camera (8.4 V and 2600 mA): approximately 2.5 hours.  
* Battery life for the Arduino board (4.2 V and 5200 mA): approximately 16 hours. 

This means we need to be careful with the batteries for the 360° servo and the HUSKYLENS module because they may fail due to a lack of power.  

Based on this estimate and the availability of batteries in our class, we chose the Samsung ICR18650-26FU model. The main features of this model are: 

The batteries that power the board are placed in a dedicated space on the 3D-printed chassis. Initially, in the prototype with the foam board base, they were glued to the bottom of the base, as seen in the initial sketches of the component layout. Later, it was decided to create a custom-made 3D-printed space for them in that same location. 

The batteries that power the servo, being a last-minute modification, have been placed in a foam board structure on the upper rear of the robot. This also extends the parking length and allows us to exit the parking space in the obstacle course with more room to maneuver.  

To power the HUSKYLENS module, an LM7805 regulator has been included to step down the voltage from the batteries from 8.4 V to 5 V. Electrolytic capacitors have also been included as recommended by the manufacturer. 

#### Wiring Scheme
The wiring diagram used for assembling the robot is shown in the image below. It was created in TinkerCad based on previous experience using this program. Some components were not available in TinkerCad, so similar ones that met the necessary connection requirements were used, and their names were noted on the final diagram to avoid confusion:



#### Sensors

The robot receives data from three main components: the Arduino R4 Minima board, the HC-SR04 sensors, and the HUSKYLENS module.  

The Arduino R4 Minima board was chosen because it has additional pins that other Arduino boards do not have, ensuring there are enough pins to connect all the components. However, after an accident in which this board stopped working, we considered replacing it with an Arduino R4 Wi-Fi board we had in class, without using the Wi-Fi and Bluetooth functions, since that would violate the rules. In the end, we used another Arduino UNO R4 Minima board and attached a shield to it so we could access all the pins we had before.  

<div align="center"><table>
 <tr>
  <td align="center" width="50%">
   
 </td>
 <td align="center" width="50%">
 
 </td>  
 </tr>
</table></div>

The HC-SR04 sensors were chosen after considering three types of sensors: the HC-SR04, the CJVL53L0XV2 (which use lasers), and the TOF10120 (which also use lasers). Initially, the CJVL53L0XV2 was chosen, although it was later replaced due to programming issues. The HC-SR04, although less efficient, is easier to program, and we had used it before.  

We started by installing three sensors (two on the sides and one at the front), because we thought that would be enough to park and navigate turns without any problems. However, adding a fourth sensor—mounted on the lower rear of the robot—provided more accurate measurements that helped us overcome challenges (specifically the parking portion of the obstacle course) more easily.  

<div align="center"><table>
  <tr>
   <td align="center" width="50%">
    
   </td>
   <td align="left" width="50%">
    <ul>
<li>Operating Voltage: 5V DC </li>
<li>Quiescent Current: < 2mA </li>
<li>Operating Current: 15mA </li>
<li>Measuring Range: 2–450 cm </li>
<li>Accuracy: ±3 mm </li>
<li>Beam Angle: 15° </li>
<li>Ultrasonic Frequency: 40 kHz </li>
<li>Minimum TRIG trigger pulse duration (TTL level): 10 μs </li>
<li>Output ECO pulse duration (TTL level): 100–25,000 μs </li>
<li>Dimensions: 45 × 20 × 15 mm </li>
<li>Minimum wait time between one measurement and the start of the next: 20 ms (50 ms recommended) </li>
</ul>
</td>
</tr>
</table></div>

The HUSKYLENS module identifies traffic light colors to navigate around them on the correct side. This module was new to us, so we had to meticulously study its features and how to program it. The most appropriate mode for this challenge is color detection. However, 70% of the time it confused the pink of the parking lot with the red of the traffic lights, which caused serious programming issues.  

One major issue it caused was that it sometimes interfered with other robot components. For example, while it was connected, the 360-degree servo wouldn’t rotate properly and would jam, but when it was disconnected, the servo rotated more smoothly

</details>

<details>
<summary><b>6.2 Current Power and Sensor Architecture</b></summary>
<br>

#### Power Supply 
The robot runs on four Samsung ICR18650-26FU batteries. Two of the batteries directly power the two mini-servos (the one on the HUSKYLENS module and the steering servo), the TF-Mini S sensor, and the Raspberry Pi Pico 2 board, while the other two power the drive servo and the HUSKYLENS.

An energy calculation was performed, taking all components into account, to help select the batteries:
<table style="border-collapse: collapse; width: 100%;">
  <thead>
    <tr>     
      <!-- Cabecera principal dividida en dos grandes columnas -->
      <th colspan="3" align="center" style="background-color: #f6f8fa; border: 1px solid #dfe2e5; padding: 10px;">Battery one🔋(the one on the wing)</th>
      <th colspan="3" align="center" style="background-color: #f6f8fa; border: 1px solid #dfe2e5; padding: 10px;">Battery two⚡(the one underneath the chassis)</th>
    </tr>
    <tr>
      <!-- Subcolumnas para la Batería 1 -->
      <th style="border: 1px solid #dfe2e5; padding: 8px;">Electronic device</th>
      <th style="border: 1px solid #dfe2e5; padding: 8px;">milliampere-hours consumed (mA/h)</th>
      <th style="border: 1px solid #dfe2e5; padding: 8px;">Volts (V)</th>
      <!-- Subcolumnas para la Batería 2 -->
      <th style="border: 1px solid #dfe2e5; padding: 8px;">Electronic device</th>
      <th style="border: 1px solid #dfe2e5; padding: 8px;">milliampere consumed (mA)</th>
      <th style="border: 1px solid #dfe2e5; padding: 8px;">volts (V)</th>
    </tr>
  </thead>
  <tbody>
    <tr>
      <!-- Fila 1 -->
      <td style="border: 1px solid #dfe2e5; padding: 6px;">Raspberry Pi Pico 2 board</td>
      <td style="border: 1px solid #dfe2e5; padding: 6px;">40 mA</td>
      <td style="border: 1px solid #dfe2e5; padding: 6px;">3,3 V</td>
      <td style="border: 1px solid #dfe2e5; padding: 6px;">360° continuous rotation servo</td>
      <td style="border: 1px solid #dfe2e5; padding: 6px;">700 mA</td>
      <td style="border: 1px solid #dfe2e5; padding: 6px;">8,4 V</td>
    </tr>
    <tr>
      <!-- Fila 2 -->
      <td style="border: 1px solid #dfe2e5; padding: 6px;">TOF400F (right and left)</td>
      <td style="border: 1px solid #dfe2e5; padding: 6px;">40 mA</td>
      <td style="border: 1px solid #dfe2e5; padding: 6px;">3,3 V</td>
      <td style="border: 1px solid #dfe2e5; padding: 6px;">HUSKYLENS module</td>
      <td style="border: 1px solid #dfe2e5; padding: 6px;">230–420 mA</td>
      <td style="border: 1px solid #dfe2e5; padding: 6px;">5 V</td>
    </tr>
    <tr>
      <!-- Fila 3 -->
      <td style="border: 1px solid #dfe2e5; padding: 6px;">LEDS</td>
      <td style="border: 1px solid #dfe2e5; padding: 6px;">15 mA</td>
      <td style="border: 1px solid #dfe2e5; padding: 6px;">3,3 V</td>
      <td style="border: none;"></td>
      <td style="border: none;"></td>
      <td style="border: none;"></td>
    </tr>
    <tr>
      <!-- Fila 4 -->
      <td style="border: 1px solid #dfe2e5; padding: 6px;">TFmini-S</td>
      <td style="border: 1px solid #dfe2e5; padding: 6px;">140 mA</td>
      <td style="border: 1px solid #dfe2e5; padding: 6px;">5 V</td>
      <td style="border: none;"></td>
      <td style="border: none;"></td>
      <td style="border: none;"></td>
    </tr>
    <tr>
      <!-- Fila 5 -->
      <td style="border: 1px solid #dfe2e5; padding: 6px;">180 microservo direction</td>
      <td style="border: 1px solid #dfe2e5; padding: 6px;">200 mA</td>
      <td style="border: 1px solid #dfe2e5; padding: 6px;">5 V</td>
      <td style="border: none;"></td>
      <td style="border: none;"></td>
      <td style="border: none;"></td>
    </tr>
    <tr>
      <!-- Fila 6 -->
      <td style="border: 1px solid #dfe2e5; padding: 6px;">10DOF magnetometer</td>
      <td style="border: 1px solid #dfe2e5; padding: 6px;">6 mA</td>
      <td style="border: 1px solid #dfe2e5; padding: 6px;">3,3 V</td>
      <td style="border: none;"></td>
      <td style="border: none;"></td>
      <td style="border: none;"></td>
    </tr>
    <tr>
      <!-- Fila 7 -->
      <td style="border: 1px solid #dfe2e5; padding: 6px;">Huskylens and TFmini micro-servo</td>
      <td style="border: 1px solid #dfe2e5; padding: 6px;">200 mA</td>
      <td style="border: 1px solid #dfe2e5; padding: 6px;">5 V</td> 
      <td style="border: none;"></td>
      <td style="border: none;"></td>
      <td style="border: none;"></td>
    </tr>
    <tr>
      <!-- Fila 8 -->
      <td style="border: 1px solid #dfe2e5; padding: 6px;">RGB sensor TCS34725</td>
      <td style="border: 1px solid #dfe2e5; padding: 6px;">6 mA</td>
      <td style="border: 1px solid #dfe2e5; padding: 6px;">3,3 V</td> 
      <td style="border: none;"></td>
      <td style="border: none;"></td>
      <td style="border: none;"></td>
    </tr>
  </tbody>
</table>

* Total: approximately 1,600 mA

Based on this data, the approximate theoretical battery life would be:

* Battery life for the traction servo and the HUSKYLENS camera (8.4 V and 2,600 mAh): approximately 2,5 hours.
* Battery life for the Raspberry Pi Pico 2 board, TFmini-S sensor, and mini servos (4.2 V and 5,200 mAh): approximately 12 hours.

This means we need to be careful with the batteries for the 360° servo and the HUSKYLENS module, as they may fail due to a lack of power.

It’s clear that we have more than enough battery power to cover the robot’s components’ power consumption, but even so, we’ve opted to have a bit of a reserve so we don’t have to worry about recharging the batteries every so often. Normally, the batteries can last up to two or three weeks, depending on whether I use it or whether we carry out a lot of tests with the robot.

Given this budget and the availability of batteries in our category, we chose the Samsung ICR18650-26FU model. The main features of this model are:

<div align="center"><table>
  <tr>
    <td align="center" width="50%">
      
    </td>
    <td align="left" width="50%">
      <ul>
        <li>Brand: Samsung</li>
        <li>Model: ICR 18650-26FU</li>
        <li>Capacity: Nominal capacity: 2600 mAh</li>
        <li>Voltage: 3.7 V nominal</li>
        <li>Charging: 4.2 V maximum, 1300 mA standard, 2600 mA maximum</li>
        <li>Discharge: Cut-off at 2.75 V, standard 520 mA, maximum 5200 mA</li>
        <li>Description: Pink cell casing, white insulating ring, 18650 format</li>
      </ul>
    </td>
  </tr>
</table></div>

The batteries that power the HUSKYLENS and the drive servo are housed in a battery expansion module on the bottom of the chassis. This way, you simply remove them and insert new ones when the battery runs out. Previously, they were placed in a dedicated space inside the 3D-printed chassis. Initially, in the prototype with a foam board base, they were glued to the bottom of the base, as can be seen in the initial sketches of the component layout. Later, it was decided to create a custom 3D-printed compartment for them in that same location.

<div align="center"><table>
  <tr>
    <td align="center" width="33%">
      
    </td>
    <td align="center" width="33%">
       
     </td>
     <td align="center" width="33%">
       
     </td>
  </tr>
</table></div>

As a last-minute modification, the batteries that power the Raspberry Pi Pico 2 board, the two microservos, and the TFmini-S sensor have been mounted on a 3D-printed structure at the top rear of the robot, inside a battery expansion module; this way, if some batteries run out, there’s no need to waste time disassembling the entire circuit to replace them—you simply remove them from there and swap them out. Additionally, this structure also expands the parking space, giving us more room to maneuver during the obstacle course. Initially, this structure was made of foam board, but it was eventually modified to use a more durable material.

<div align="center"><table>
  <tr>
    <td align="center" width="33%">
      
    </td>
    <td align="center" width="33%">
      
    </td>
    <td align="center" width="33%">
      
    </td>
  </tr>
</table></div>

To power the HUSKYLENS module, an LM7805 regulator has been included to step down the voltage from the batteries from 8.4 V to 5 V. Electrolytic capacitors have also been included as recommended by the manufacturer. 

<div align="center"><table>
  <tr>
    <td align="center" width="33%">
      
    </td>
  </tr>
</table></div>

#### Wiring Scheme
The wiring diagram was created in Cirkit Designer. In previous versions, it was created in TinkerCad, but the components we used weren’t available there, and since Cirkit Designer allows you to design custom components, we created it there instead. Here is the final result:


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

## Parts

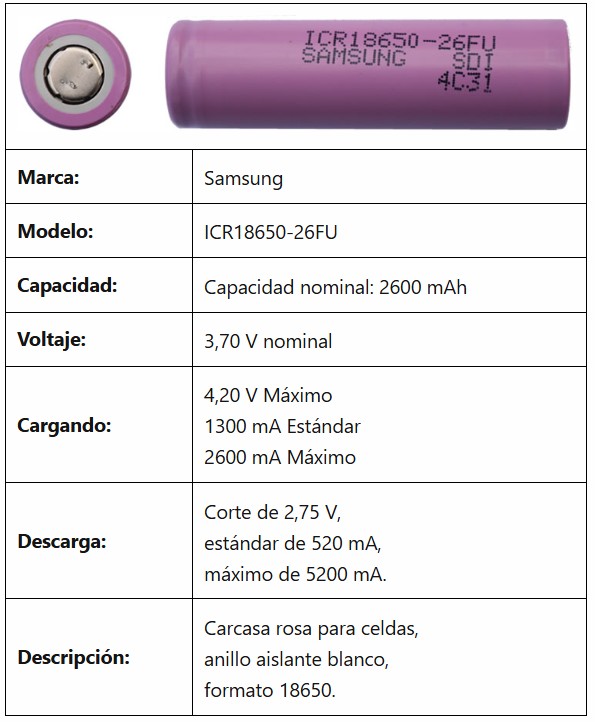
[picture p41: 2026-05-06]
other/components/BATERIAS_SAMSUNG.jpg

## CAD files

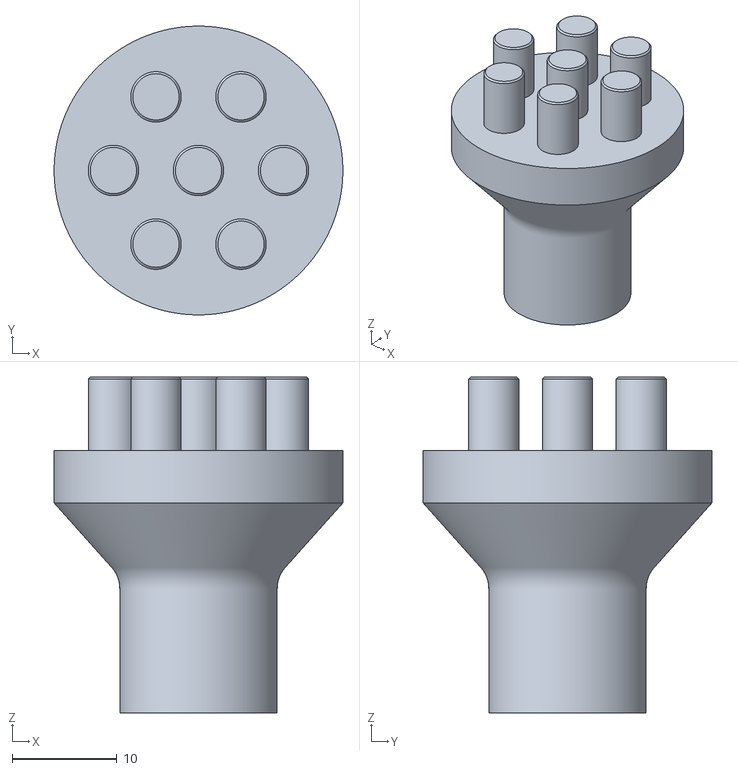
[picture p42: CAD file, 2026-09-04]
models/wheel adapter.stl
27.5 x 27.5 x 32.0

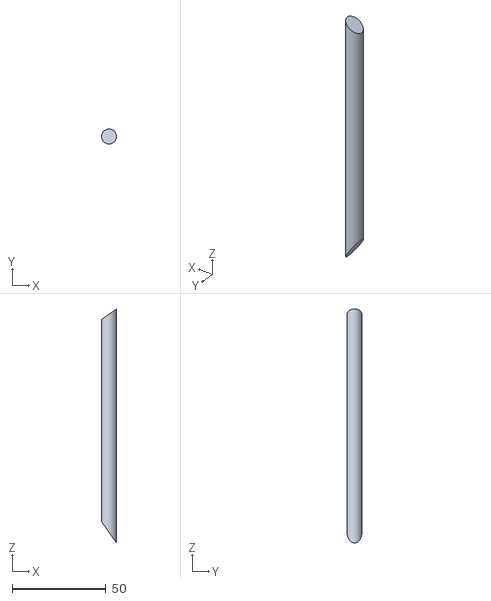
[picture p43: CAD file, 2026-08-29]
models/SOPORTE_10-DOF.stl
8.00 x 8.00 x 125.0

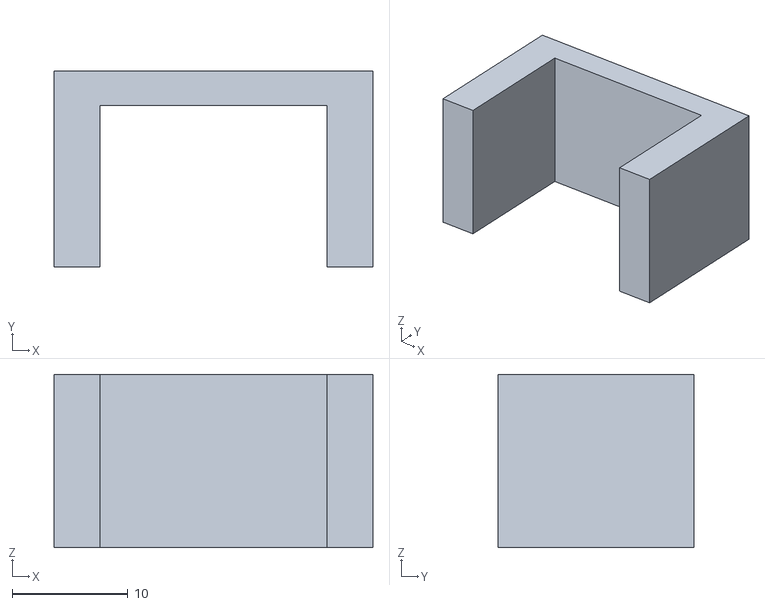
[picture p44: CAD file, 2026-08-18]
models/SOPORTE_INTERRUPTOR.stl
27.6 x 17.0 x 15.0

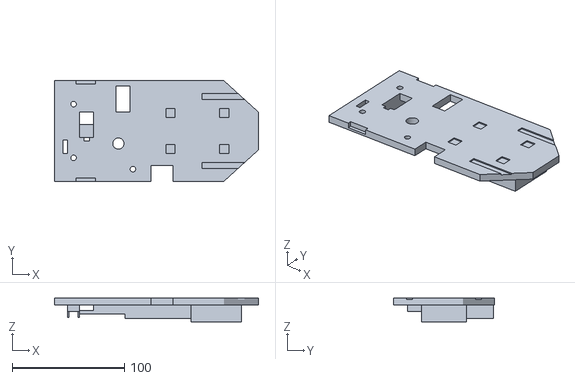
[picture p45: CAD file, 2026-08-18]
models/CHASIS_modificado_2.stl
182.0 x 90.0 x 21.0

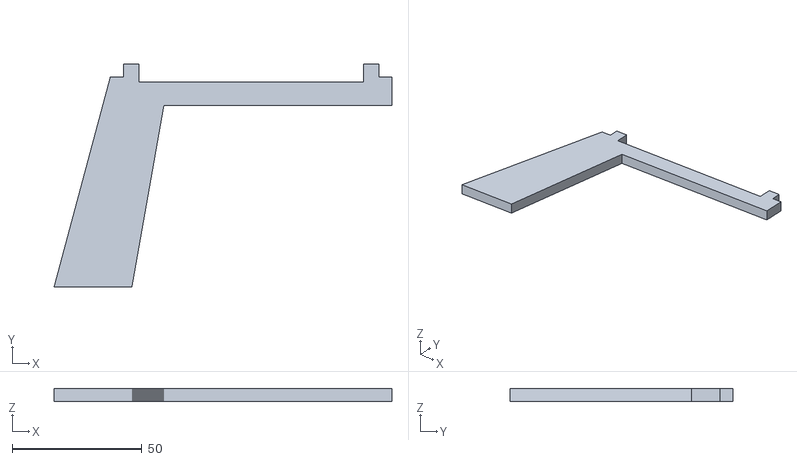
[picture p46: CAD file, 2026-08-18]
models/soportebateria1.stl
130.2 x 86.0 x 5.00

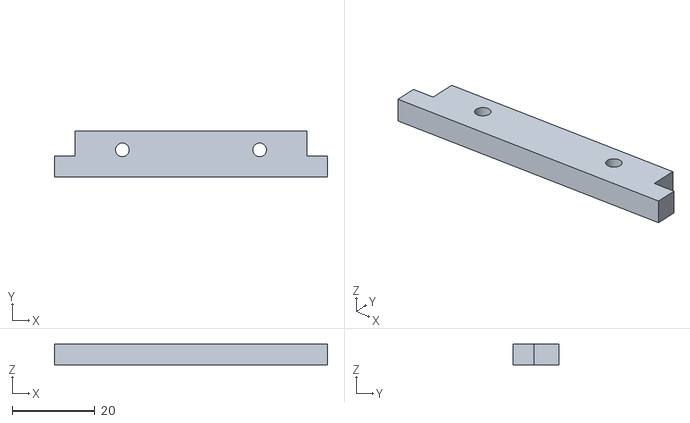
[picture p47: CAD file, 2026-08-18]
models/soportebateria2.stl
66.0 x 11.0 x 5.00

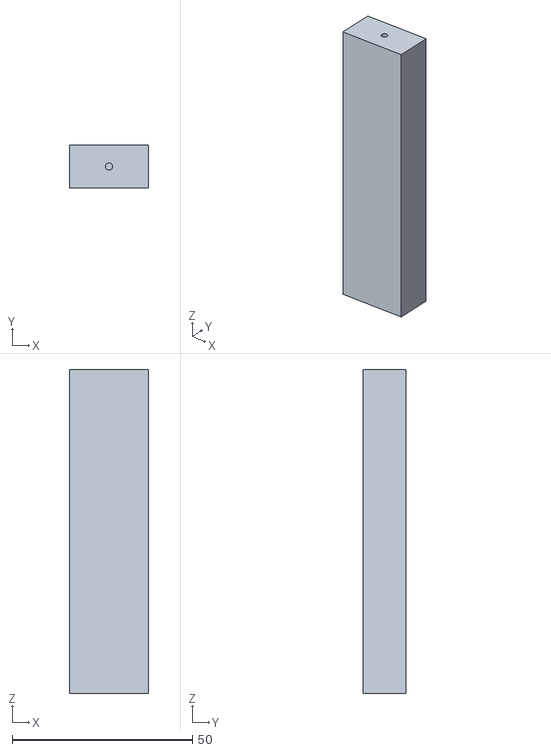
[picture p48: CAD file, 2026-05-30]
models/HUSKYLENS_SUPPORT.stl
22.0 x 12.0 x 90.0

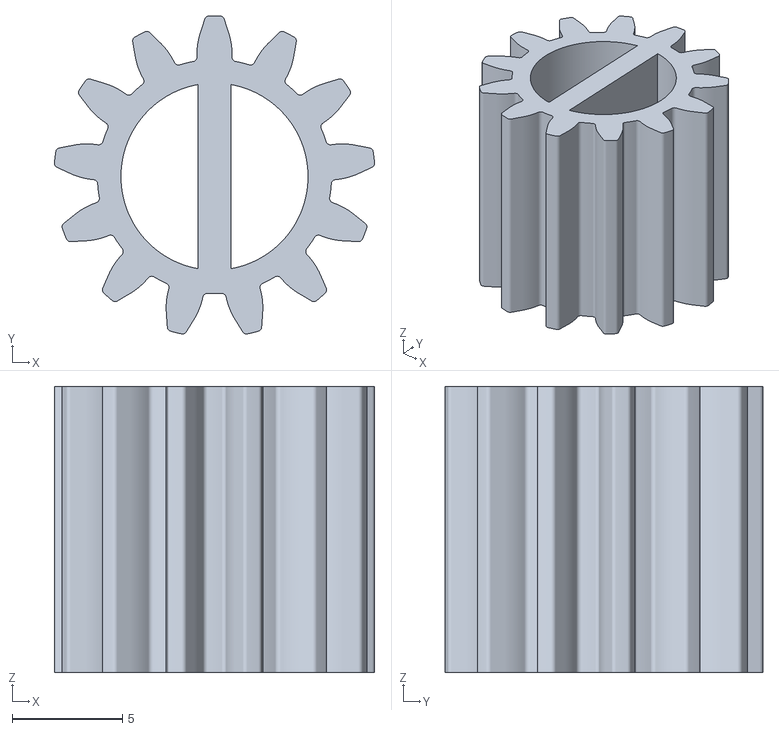
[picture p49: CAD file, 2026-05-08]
models/GEAR_ADAPTER.stl
14.6 x 14.5 x 13.0

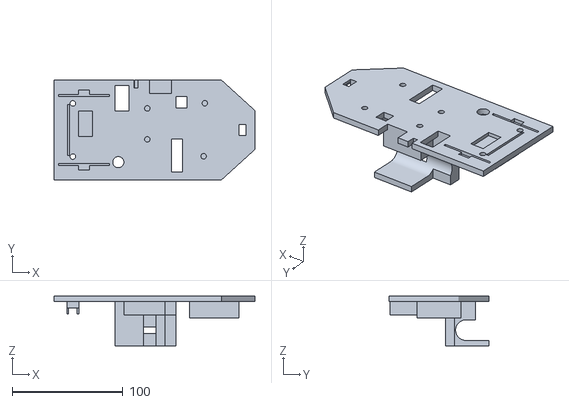
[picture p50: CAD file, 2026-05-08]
models/CHASSIS.stl
181.2 x 90.0 x 45.0

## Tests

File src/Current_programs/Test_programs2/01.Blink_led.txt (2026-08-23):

# Programa Blink para pi pico utilizando MicroPython
from machine import Pin
import time

# Configura el GPIO 16 como salida digital
led_externo = Pin(16, Pin.OUT)

print("¡Programa Blink Iniciado con éxito!")

while True:
    led_externo.value(1) # Enciende el LED (3.3V)
    print("LED Encendido")
    time.sleep(1)
    
    led_externo.value(0) # Apaga el LED (0V)
    print("LED Apagado")
    time.sleep(1)

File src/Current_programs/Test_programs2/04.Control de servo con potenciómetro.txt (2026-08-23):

#Control de servo con potenciómetro.

from machine import Pin, ADC, PWM
import time

# 1. Configuración del Potenciómetro en el GPIO 28 (ADC canal 2)
potenciometro = ADC(Pin(28))

# 2. Configuración del Servo en el GPIO 10 usando PWM
servo = PWM(Pin(10))
servo.freq(50) # Los servos estándar funcionan estrictamente a 50Hz

# Función matemática idéntica al "map" de Arduino
def mapear(valor, desde_min, desde_max, hacia_min, hacia_max):
    return int((valor - desde_min) * (hacia_max - hacia_min) / (desde_max - desde_min) + hacia_min)

print("--- Control de Servo con Potenciómetro Iniciado ---")

while True:
    # Leer el potenciómetro (Rango nativo de la Pico 2: 0 a 65535)
    lectura_pot = potenciometro.read_u16()
    
    # Mapeamos la lectura para el Monitor Serie (0 a 1023 como en tu Arduino)
    joy_x = mapear(lectura_pot, 0, 65535, 0, 1023)
    
    # Mapeamos la lectura directamente a los valores de PWM que entiende el servo (0° a 180°)
    # 1638 equivale a 0.5ms (0 grados) y 8192 equivale a 2.5ms (180 grados)
    pulso_servo = mapear(lectura_pot, 0, 65535, 1638, 8192)
    
    # Mapeamos también a grados puros solo para mostrarlo de forma bonita en la terminal
    grados = mapear(lectura_pot, 0, 65535, 0, 180)
    
    # Enviamos la señal PWM al servo para que se mueva
    servo.duty_u16(pulso_servo)
    
    # Imprimir en la terminal simulando tu Serial.print de Arduino
    print(f"JOYx={joy_x}   Grados={grados}º   PWM={pulso_servo}")
    
    # Pausa de 100 milisegundos idéntica a tu delay(100)
    time.sleep_ms(100)

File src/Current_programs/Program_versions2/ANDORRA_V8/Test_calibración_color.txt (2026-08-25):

"""
TEST STANDALONE - Calibracion del sensor de color TCS34725
Imprime r, g, b, claro en bucle continuo. Pasar el sensor sobre cada
superficie (blanco del tapete, linea naranja, linea azul, y alguno de los
baches/zonas grises que dan falsos positivos) y anotar los rangos
para cada una.
"""
from machine import Pin, I2C
from tcs34725 import TCS34725
import time

i2c0 = I2C(0, sda=Pin(4), scl=Pin(5))
sensor_color = TCS34725(i2c0)
print("Sensor listo. Pasando a lectura continua...")

while True:
    r, g, b, claro = sensor_color.read_rgbc()
    total = r + g + b
    if total > 0:
        pr = r / total
        pg = g / total
        pb = b / total
        print(f"r={r:4d} g={g:4d} b={b:4d} claro={claro:4d}  |  r%={pr:.2f} g%={pg:.2f} b%={pb:.2f}")
    else:
        print(f"r={r:4d} g={g:4d} b={b:4d} claro={claro:4d}  |  (total=0)")
    time.sleep_ms(200)

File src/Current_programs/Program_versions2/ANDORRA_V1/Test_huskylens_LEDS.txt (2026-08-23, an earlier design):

"""
TEST STANDALONE - Huskylens + LEDs
Enciende el LED VERDE si ve un bloque ID2 (verde) y el LED ROJO si ve un
bloque ID1 (rojo). Si ve los dos a la vez, enciende los dos.
Requiere subir tambien huskylens.py a la Pico.

Conexion:
  SDA1 -> GPIO14
  SCL1 -> GPIO15
"""

from machine import Pin, I2C
from huskylens import HuskyLens
import time

ledV = Pin(10, Pin.OUT)
ledR = Pin(22, Pin.OUT)

i2c1 = I2C(1, sda=Pin(14), scl=Pin(15), freq=100000, timeout=100000)
hl = HuskyLens(i2c1)

print("Dispositivos I2C1 encontrados:", [hex(a) for a in i2c1.scan()])
print("Knock:", hl.knock())

while True:
    bloques = hl.get_blocks()

    hay_rojo = any(b.id == 1 for b in bloques)
    hay_verde = any(b.id == 2 for b in bloques)

    ledR.value(1 if hay_rojo else 0)
    ledV.value(1 if hay_verde else 0)

    time.sleep_ms(100)

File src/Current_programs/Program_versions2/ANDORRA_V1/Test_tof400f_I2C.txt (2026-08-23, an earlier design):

"""
TEST STANDALONE - TOF400F #2 (VL53L1X) por I2C1
Requiere subir tambien vl53l1x.py a la Pico.

Conexion:
  SDA1 -> GPIO14
  SCL1 -> GPIO15
"""

from machine import Pin, I2C
from vl53l1x import VL53L1X
import time

i2c1 = I2C(1, sda=Pin(14), scl=Pin(15), freq=100000, timeout=100000)

print("Dispositivos I2C1 encontrados:", [hex(a) for a in i2c1.scan()])

try:
    tof2 = VL53L1X(i2c1, address=0x29)
    print("TOF400F #2 listo.")
except Exception as e:
    print("Error al iniciar TOF400F #2:", e)
    tof2 = None

while tof2 is not None:
    d = tof2.read_distance_mm()
    if d is not None:
        print("Distancia: %d mm (%.1f cm)" % (d, d / 10))
    time.sleep_ms(50)

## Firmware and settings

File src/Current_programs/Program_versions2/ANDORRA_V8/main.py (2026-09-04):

#Descomponemos el programa en varios archivos para que sea más legible y mantenible.
#Retocamos la lectura de las líneas de suelo. Ahora va por color.
#Reforzamos la lectura de los sensores de distancia. Ahora se leen varias veces y se descartan lecturas erráticas.
#Cambiamos la forma de detectar misión 1 - misión 2. Ahora se hace por distancias laterales en lugar de por color de línea.
#Introducimos el magnetómetro 10 DOF
#Troceamos funciones_comunes.py en 3 archivos para manejarlos mejor
#Hemos podido completar la primera vuelta de la zona de obstáculos.Ahora vamos a hacer que el robot no confunda el parking con un bloque rojo.
#Decidimos cambiar estrategia. Eliminamos paredes aparcamiento.Implementamos misión 4.



"""MAIN.PY - Punto de entrada. Arranque unificado para las 4 misiones: ya no
hay dos zonas de salida distintas, las cuatro empiezan igual (retroceso +
comprobacion de pilar de frente + busqueda de esquina si no hay pilar)."""
import time
import hardware
from funciones_comunes import leer_tfmini, leer_tof_derecho_mm, medir_rumbos_calles, pulso_barrido, _obtener_bloques, _mejor_bloque
from funciones_comunes1 import buscar_pilar
from mision1_cw import ejecutar_mision_1_cw
from mision2_ccw import ejecutar_mision_2_ccw
from mision3_cw import ejecutar_mision_3_cw
from mision4_ccw import ejecutar_mision_4_ccw

# ==========================================
# FASE DE INICIO (ESPERA DE BOTON)
# ==========================================
print("--- Robot Unificado Inicializado ---")
hardware.servoTraccion.duty_u16(hardware.Para)
hardware.servoDireccion.duty_u16(hardware.Recto)
hardware.SERVOcam.duty_u16(hardware.Cam_Centro)

while hardware.pinBoton.value() == 0:
    hardware.ledR.value(1)
    hardware.ledV.value(0)
    time.sleep_ms(100)
    hardware.ledR.value(0)
    hardware.ledV.value(1)
    time.sleep_ms(100)

hardware.ledV.value(0)
hardware.ledR.value(0)
print("--- ¡ARRANQUE INTERNO! ---")

# ==========================================
# RETROCESO INICIAL (sale del hueco de salida, comun a las 4 misiones)
# ==========================================
hardware.servoDireccion.duty_u16(hardware.Recto)
hardware.servoTraccion.duty_u16(hardware.Retrocede_lento)
time.sleep_ms(hardware.TIEMPO_RETROCESO_INICIAL_MS)
hardware.servoTraccion.duty_u16(hardware.Para)

# ==========================================
# COMPROBACION 1: pilar visible de frente -> Mision 3/4 directa
# ==========================================
hardware.SERVOcam.duty_u16(pulso_barrido(0))
time.sleep_ms(300)
bloques = _obtener_bloques()

if len(bloques) > 0:
    objetivo = _mejor_bloque(bloques)

    if objetivo.x_center > hardware.FRAME_CENTRO_X:
        print("COMPROBACION 1: pilar a la derecha -> MISION 3 directa")
        hardware.color_esquina = 'NARANJA'
        if hardware.mag is not None:
            medir_rumbos_calles(hardware.GIRO_POR_ESQUINA_DEG)
        ejecutar_mision_3_cw(angulo_inicial=0, color_inicial=objetivo.id)
    else:
        print("COMPROBACION 1: pilar a la izquierda -> MISION 4 directa")
        hardware.color_esquina = 'AZUL'
        if hardware.mag is not None:
            medir_rumbos_calles(-hardware.GIRO_POR_ESQUINA_DEG)
        ejecutar_mision_4_ccw(angulo_inicial=0, color_inicial=objetivo.id)

else:
    # ==========================================
    # BUSQUEDA DE ESQUINA (sin pilar de frente): igual que el antiguo Reto
    # Libre - avanza leyendo TOF derecho + TFmini izquierdo hasta ver el hueco.
    # ==========================================
    hardware.SERVOcam.duty_u16(hardware.RADAR_FIJO_IZQUIERDA)
    time.sleep_ms(300)

    while hardware.uart0.any():
        hardware.uart0.read(hardware.uart0.any())
    time.sleep_ms(10)

    hardware.servoDireccion.duty_u16(hardware.Recto)
    hardware.servoTraccion.duty_u16(hardware.Avanza_tope)

    lado_hueco = None
    while lado_hueco is None:
        dist_der_mm = leer_tof_derecho_mm()
        dist_izq_cm = leer_tfmini()

        if dist_der_mm is not None and (dist_der_mm / 10) > hardware.DISTANCIA_HUECO_CM:
            lado_hueco = 'derecha'
        elif dist_izq_cm is not None and dist_izq_cm > hardware.DISTANCIA_HUECO_CM:
            lado_hueco = 'izquierda'

        time.sleep_ms(20)

    hardware.contadorLineas = 1  # primera esquina ya contada, igual que antes

    if hardware.mag is not None:
        signo = hardware.GIRO_POR_ESQUINA_DEG if lado_hueco == 'derecha' else -hardware.GIRO_POR_ESQUINA_DEG
        medir_rumbos_calles(signo)

    if lado_hueco == 'derecha':
        hardware.SERVOcam.duty_u16(hardware.RADAR_FIJO_DERECHA)
        print("Movimiento Inicial 1: Avanzando a la derecha...")
        hardware.servoDireccion.duty_u16(3900)
        hardware.servoTraccion.duty_u16(4000)
        time.sleep_ms(2100)
        hardware.servoTraccion.duty_u16(hardware.Para)

        angulo, color = buscar_pilar(hardware.ANGULO_BUSQUEDA_TRANSICION, -hardware.ANGULO_BUSQUEDA_TRANSICION,
                                      paso=hardware.PASO_BARRIDO)
        if angulo is not None:
            print("BARRIDO ESTRECHO: pilar encontrado -> MISION 3")
            hardware.color_esquina = 'NARANJA'
            ejecutar_mision_3_cw(angulo_inicial=angulo, color_inicial=color)
        else:
            print("BARRIDO ESTRECHO: nada -> MISION 1")
            ejecutar_mision_1_cw(saltar_movimiento_1=True)
    else:
        hardware.SERVOcam.duty_u16(hardware.RADAR_FIJO_IZQUIERDA)
        print("Movimiento Inicial 1: Avanzando a la izquierda...")
        hardware.servoDireccion.duty_u16(6190)
        hardware.servoTraccion.duty_u16(4000)
        time.sleep_ms(1200)
        hardware.servoTraccion.duty_u16(hardware.Para)

        angulo, color = buscar_pilar(hardware.ANGULO_BUSQUEDA_TRANSICION, -hardware.ANGULO_BUSQUEDA_TRANSICION,
                                      paso=hardware.PASO_BARRIDO)
        if angulo is not None:
            print("BARRIDO ESTRECHO: pilar encontrado -> MISION 4")
            hardware.color_esquina = 'AZUL'
            ejecutar_mision_4_ccw(angulo_inicial=angulo, color_inicial=color)
        else:
            print("BARRIDO ESTRECHO: nada -> MISION 2")
            ejecutar_mision_2_ccw(saltar_movimiento_1=True)

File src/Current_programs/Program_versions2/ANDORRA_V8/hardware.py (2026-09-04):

"""
HARDWARE.PY - Configuracion centralizada del robot.
Pines, actuadores, sensores, constantes de calibracion y estado compartido
entre misiones (contadorLineas, sobre_linea).

Todos los demas modulos (funciones_comunes.py, mision1_cw.py, etc.) importan
este archivo con "import hardware" y acceden a todo con el prefijo hardware.,
por ejemplo hardware.uart0, hardware.Recto, hardware.contadorLineas.

Esto es necesario porque las variables de estado (contadorLineas, sobre_linea)
se modifican desde varios modulos - "from hardware import contadorLineas"
NO funcionaria para eso, porque crearia una copia local en vez de modificar
el original. Con "import hardware" y "hardware.contadorLineas = ...", todos
los modulos comparten el mismo valor real.
"""
from machine import Pin, UART, PWM, I2C
import time
from tcs34725 import TCS34725
from vl53l1x import VL53L1X
from huskylens import HuskyLens
from lsm303_mag import LSM303Mag

# ==========================================
# 1. CONFIGURACION DE PINES
# ==========================================
pinBoton = Pin(2, Pin.IN, Pin.PULL_DOWN)
ledV = Pin(10, Pin.OUT)
ledR = Pin(22, Pin.OUT)

# Comunicacion UART0 para el LiDAR TFmini-S (frontal)
uart0 = UART(0, baudrate=115200, tx=Pin(0), rx=Pin(1))

# Comunicacion UART1 para el TOF400F derecho (sigue en modo Modbus/Serie de fabrica)
uart1 = UART(1, baudrate=115200, tx=Pin(8), rx=Pin(9))

# Comunicacion I2C1 para el TOF400F #2 (reconfigurado a modo IIC) -> lateral IZQUIERDO
# y la Huskylens, que comparten el mismo bus fisico (direcciones distintas: 0x29 y 0x32).
i2c1 = I2C(1, sda=Pin(14), scl=Pin(15), freq=100000, timeout=100000)
try:
    tof_izquierdo = VL53L1X(i2c1, address=0x29)
    print("TOF400F izquierdo (I2C) listo!")
except Exception as e:
    print("Error TOF400F izquierdo:", e)
    tof_izquierdo = None

husky = HuskyLens(i2c1)
husky_lista = False
for _intento in range(5):
    if husky.knock():
        husky_lista = True
        break
    time.sleep_ms(300)  # la Huskylens puede tardar en terminar de arrancar

if husky_lista:
    print("Huskylens lista!")
else:
    print("Aviso: Huskylens no respondio al knock tras varios intentos (se seguira intentando usar)")

# Inicializar bus I2C0 para el sensor de color y el magnetometro
i2c0 = I2C(0, sda=Pin(4), scl=Pin(5))
try:
    sensor_color = TCS34725(i2c0)
    print("¡Sensor TCS34725 listo!")
except Exception as e:
    print("Error sensor color:", e)
    sensor_color = None

try:
    mag = LSM303Mag(i2c0)
    print("Magnetometro listo!")
except Exception as e:
    print("Error magnetometro:", e)
    mag = None

# Actuadores (PWM a 50Hz)
servoTraccion = PWM(Pin(13))    # Movido del pin 14 al 13 (14 ahora es SDA1)
servoDireccion = PWM(Pin(20))
SERVOcam = PWM(Pin(21))

servoTraccion.freq(50)
servoDireccion.freq(50)
SERVOcam.freq(50)

# ==========================================
# 2. CONSTANTES DE CALIBRACION REALES
# ==========================================
# Servo Direccion
Recto = 4950
Dcha = 3900
Izda = 6190

# Servo Camara / Lidar (Pin 21)
Cam_Centro = 4675
RADAR_FIJO_DERECHA = 1350
RADAR_FIJO_IZQUIERDA = 8000

# Servo Traccion (Rotacion continua)
Para = 4900
Avanza_tope = 3200
Avanza_lento = 4200           # AJUSTAR EN PISTA: velocidad reducida mientras se alinea con el objetivo
Avanza_crucero = 3700         # AJUSTAR EN PISTA: velocidad durante navegar_calle_por_rumbo ya alineado - mas lenta que Avanza_tope para no adelantar al barrido ancho
Avanza_giro_cerrado = 4600     # AJUSTAR EN PISTA: navegar_calle_por_rumbo con error de rumbo grande o pared muy cerca - casi un giro sobre el sitio, nunca se para del todo
Retrocede_tope = 6250
Retrocede_lento = 5700         # AJUSTAR EN PISTA: velocidad reducida para el retroceso previo al esquive (no a tope, mas control)
TIEMPO_RETROCESO_INICIAL_MS = 2000  # AJUSTAR EN PISTA: retroceso inicial comun a las 4 misiones, antes de decidir cual toca
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

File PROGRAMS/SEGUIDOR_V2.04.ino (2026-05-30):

#include <HUSKYLENS.h>  //Cable verde al A4  y   cable azul al A5
#include <Wire.h>
HUSKYLENS huskylens;
const int rojo = 1;
const int verde = 2;

#include <HCSR04.h>
HCSR04 hc(2, new int[4]{3, 4, 5, 7}, 4); //initialisation class HCSR04 (trig pin , echo pin, number of sensor)

#include <Servo.h>
Servo servoTraccion;
Servo servoDireccion;
Servo SERVOcam;

#define ledV 14
#define ledR 15

int i=0;
int dir=90;     
int distDE=15;  // SENSOR 0 derecho
int distFR=110; // SENSOR 1 frontal
int distIZ=15;  // SENSOR 2 izquierdo
int distTR=15;  // SENSOR 3 trasero

// Variables control servos
int Izda=134;
int Dcha=54;
int Recto=94;
int Para=90;
int Avanza=0;
int Retrocede=180;
int lectura=0;
int CASO;

//variable para esquivar obstáculos.
int ladoBusqueda = 1; // 1 = empezar zig-zag a la derecha, 2 = empezar a la izquierda

//variables para contar vueltas en el desafío libre.
int contadorLineas = 0;              // guarda las lineas rojas que va cruzando
unsigned long tiempoBloqueoRojo = 0; // guarda el momento exacto en que pisa el rojo
bool rojoBloqueado = false;          // bandera para saber si esta en el tiempo de espera

void setup()
{ //Serial.begin(9600);
Wire.begin(); // Iniciar el bus I2C
pinMode (12, INPUT);
pinMode (13, OUTPUT);
pinMode(ledV, OUTPUT); //led verde
pinMode(ledR, OUTPUT);  //led rojo

servoTraccion.attach(6);  // 0 AVANZA   90 STOP    180 RETROCEDE
servoDireccion.attach(9);  // 50 DCHA   90 RECTO   130 IZDA 
SERVOcam.attach(10);      // 0 DCHA   86 RECTO   172 IZDA 
servoTraccion.write(Para);
servoDireccion.write(Recto);
SERVOcam.write(86);

while (!huskylens.begin(Wire)) {   // Con el while, el programa no continua hasta que se inicie la cámara
    //Serial.println("Error al iniciar HuskyLens");
    digitalWrite(13, HIGH);
    delay(1000);}
    digitalWrite(13, LOW);
delay(300);   
huskylens.writeAlgorithm(ALGORITHM_OBJECT_TRACKING);
delay(300);

while (digitalRead(12) == LOW) {
    digitalWrite(13, HIGH);
    delay(100);
    digitalWrite(13, LOW);
    delay(100);
  }
  
 }

void scan1(){
  while (true){
distFR=hc.dist(1);
delay(60);
if ((distFR>2)&&(distFR<250))
    {break;}
}

if (distFR > 40) {
      digitalWrite(ledV, HIGH); 
      delay(2000);
      digitalWrite(ledV, LOW);
   CASO=1;  //El robot esta en la zona de salida
   scanABIERTO();
   } 

if (distFR < 40) {
      digitalWrite(ledR, HIGH); 
      delay(2000);
      digitalWrite(ledR, LOW);
   CASO=2;   //El robot esta en el aparcamiento
   scanOBSTACULOS();
   } 
}

////////////////////zona Desafio Abierto////////////////////////////////

void scanABIERTO(){
  while (true){
servoDireccion.write(Recto);
servoTraccion.write(105); //atras despacito hasta ver el hueco con un sensor lateral
distDE=hc.dist(0);
delay(30);
distIZ=hc.dist(2);
delay(30);
if ((distDE>90)||(distIZ>90)) //detecta hueco a un lado
    { delay(30);
      servoTraccion.write(Para);
      break;}
}

if (distDE < distIZ) {
   giroCCW();
   } //CCW a izquierdas

if (distDE > distIZ) {
   giroCW();
   } //CW a derechas
}

void giroCW(){

servoDireccion.write(70);
servoTraccion.write(70);
delay(2100);
servoDireccion.write(110);
servoTraccion.write(70);
huskylens.writeAlgorithm(ALGORITHM_COLOR_RECOGNITION);
delay(2400);



while(true) {
  servoTraccion.write(0); 
  servoDireccion.write(dir);
  distDE=hc.dist(0);
  delay(30);

  dir=(80-3*(-15+distDE)); //15 es la distancia a la pared y *3 es el factor de coreección de la dirección
  dir = constrain(dir, Dcha, Izda); // Dcha<90 y Izda>90
  servoDireccion.write(dir);

  // LOGICA PARA CONTAR LAS LINEAS ROJAS DEL SUELO
  
  // si estamos en tiempo de espera miramos si ya pasaron los 3 segundos para desbloquear
  if (rojoBloqueado) {
    if (millis() - tiempoBloqueoRojo > 3000) { 
      rojoBloqueado = false; // ya pasamos la linea, volvemos a activar el sensor
    }
  }

  // si el sensor esta activo pedimos datos a la huskylens
  if (!rojoBloqueado && huskylens.request() && huskylens.available()) {
    HUSKYLENSResult colorSuelo = huskylens.read();
    
    if (colorSuelo.command == COMMAND_RETURN_BLOCK) {
      // si ve la linea roja y ademas esta en la parte baja de la pantalla (cerca del coche)
      if (colorSuelo.ID == rojo && colorSuelo.yCenter > 160) { 
        contadorLineas++; // sumamos una esquina detectada
        tiempoBloqueoRojo = millis(); // guardamos el tiempo actual
        rojoBloqueado = true; // bloqueamos el sensor para no repetir lecturas
        
        // testigo visual: parpadeo rapido del led rojo de arduino al pasar la linea
        digitalWrite(ledR, HIGH); delay(100); digitalWrite(ledR, LOW);
      }
    }
  }

  // CONTROL DE FIN DE CARRERA: si llegamos a 12 lineas (3 vueltas) el coche para
  if (contadorLineas >= 13) {
    servoTraccion.write(Para); // detiene el motor
    servoDireccion.write(Recto); // endereza ruedas
    while(true) {
      // bucle infinito de parada final de carrera
      digitalWrite(ledR, HIGH); digitalWrite(ledV, HIGH); // leds fijos de fin de carrera
    }
  }
}
}


void giroCCW(){

servoDireccion.write(110);
servoTraccion.write(70);
delay(3100);
servoDireccion.write(70);
servoTraccion.write(70);
huskylens.writeAlgorithm(ALGORITHM_COLOR_RECOGNITION);
delay(2200);
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

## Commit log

2026-05-18 Rename Arduino R4 MINIMA.jpg to ROBOT/Arduino R4 MINIMA.jpg
2026-05-18 Rename ROBOT/Arduino R4 MINIMA.jpg to Arduino R4 MINIMA.jpg
2026-05-18 Rename Arduino R4 MINIMA.jpg to COMPONENTS/Arduino R4 MINIMA.jpg
2026-05-18 Rename Captura de pantalla 2026-05-06 174801.png to COMPONENTS/Captura de pantalla 2026-05-06 174801.png
2026-05-18 Rename Captura de pantalla 2026-05-06 175044.png to COMPONENTS/Captura de pantalla 2026-05-06 175044.png
2026-05-18 Rename Circuit board.webp to COMPONENTS/Circuit board.webp
2026-05-18 Rename Arduino_R4 MINIMA.jpg to COMPONENTS/Arduino_R4 MINIMA.jpg
2026-05-18 Rename Gear adapter.png to COMPONENTS/Gear adapter.png
2026-05-18 Rename Gear teeth Lego 4285634.jpg to COMPONENTS/Gear teeth Lego 4285634.jpg
2026-05-18 Rename Lego wheels 13 x 24.jpg to COMPONENTS/Lego wheels 13 x 24.jpg
2026-05-18 Rename Lego wheels 30.4 x 14.webp to COMPONENTS/Lego wheels 30.4 x 14.webp
2026-05-18 Rename Pull down button.jpg to COMPONENTS/Pull down button.jpg
2026-05-18 Rename Rocker Switch.avif to COMPONENTS/Rocker Switch.avif
2026-05-18 Rename Samsung battery 2600mAh.webp to COMPONENTS/Samsung battery 2600mAh.webp
2026-05-18 Rename Servo 180.avif to COMPONENTS/Servo 180.avif
2026-05-18 Rename Servo MS18.jpg to COMPONENTS/Servo MS18.jpg
2026-05-18 Rename Servo arm MS18.avif to COMPONENTS/Servo arm MS18.avif
2026-05-18 Rename Wheel adapter.png to COMPONENTS/Wheel adapter.png
2026-05-18 Rename Servo 360.webp to COMPONENTS/Servo 360.webp
2026-05-18 Rename Wiring scheme.jpg to Wiring scheme.jpg
2026-05-18 Rename WHEEL_ADAPTER.stl to 3D_DESIGNS /WHEEL_ADAPTER.stl
    [WHEEL_ADAPTER.stl]
2026-05-19 Rename Adaptador_rueda.stl to 3D_DESIGNS /Adaptador_rueda.stl
    [Adaptador_rueda.stl]
2026-05-19 Rename 3D_DESIGNS /Adaptador_rueda.stl to Adaptador_rueda.stl
    [Adaptador_rueda.stl]
2026-05-30 Rename Diagrama de flujo.png to PROGRAMS/Diagrama de flujo.png
2026-05-30 Rename SERVO180_caract.jpg to OTHER /SERVO180_caract.jpg
2026-05-30 Rename SERVO360_caract.jpg to OTHER /SERVO360_caract.jpg
2026-05-30 Rename camera support 1.jpeg to OTHER /camera support 1.jpeg
2026-05-30 Rename camera support 2.jpeg to OTHER /camera support 2.jpeg
2026-05-30 Rename electric_scheme.jpg to WIRING SCHEMES /electric_scheme.jpg
2026-05-30 Rename pinout-arduino-uno-r4-minima.webp to WIRING SCHEMES /pinout-arduino-uno-r4-minima.webp
2026-05-30 Rename power bank batteries.png to COMPONENTS/power bank batteries.png
2026-05-30 Rename prototype1.1.jpg to OTHER /prototype1.1.jpg
2026-05-30 Rename prototype1.2.jpg to OTHER /prototype1.2.jpg
2026-05-30 Rename prototype1.3.jpg to OTHER /prototype1.3.jpg
2026-05-30 Rename steering_system.JPG to OTHER /steering_system.JPG
2026-05-30 Rename steering_system2.JPG to OTHER /steering_system2.JPG
2026-05-30 Rename steering_system3.JPG to OTHER /steering_system3.JPG
2026-05-30 Rename WIRING SCHEMES /electric_scheme.jpg to WIRING_SCHEMES electric_scheme.jpg
2026-05-30 Rename pinout-arduino-uno-r4-minima.webp to pinout-arduino-uno-r4-minima.webp
2026-05-30 Rename WIRING_SCHEMES electric_scheme.jpg to WIRING_SCHEMES/electric_scheme.jpg
2026-05-30 Rename pinout-arduino-uno-r4-minima.webp to pinout-arduino-uno-r4-minima.webp
